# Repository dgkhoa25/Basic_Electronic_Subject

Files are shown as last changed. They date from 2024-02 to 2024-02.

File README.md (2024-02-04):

This project is created based on a subject with topic "Basic Electronic Project" (Đồ án Điện tử căn bản).

The name of project is "Designing model weighs mass to serve for mixing cement". 

******************************** ABSTRACT ***********************************************************

In order to help minimize errors in the process of providing materials for the consolidation process, this topic will provide a solution with a model of considering the forces serving that work.
The goal of this project is to help people limit errors, shortages, or excesses of materials by using mass sensors and digital signal processing systems to give the most accurate amount of materials 
needed to supply to the mixing systems. Some of the benefits of the project are: contributing to improving the accuracy of the quantity to be used and converting between different types of cement to be 
scanned automatically, saving users time, calculate, estimate. With this model, the system will process sequentially, so an error during the run is possible if a part of the input signal goes wrong.
Compared with the manual mixing method, this system will be more efficient in speed, with an accurate output volume of about 90%.

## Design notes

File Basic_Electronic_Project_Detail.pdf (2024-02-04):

BỘ GIÁO DỤC VÀ ĐÀO TẠO
TRƯỜNG ĐẠI HỌC CẦN THƠ
TRƯỜNG BÁCH KHOA
KHOA TỰ ĐỘNG HÓA
------🙢✧🙠------

BÁO CÁO
ĐỒ ÁN ĐIỆN TỬ CĂN BẢN
Mã học phần: KC331

### THIẾT KẾ MÔ HÌNH HỆ THỐNG CÂN ĐỊNH LƯỢNG PHỤC VỤ CHO PHA TRỘN XI MĂNG

CÁN BỘ HƯỚNG DẪN | SINH VIÊN THỰC HIỆN
TS. Nguyễn Hoàng Dũng | Nguyễn Đăng Khoa B1907027

Tháng 04/2023

Đồ án Điện tử căn bản | Trường Đại học Cần Thơ

### THIẾT KẾ MÔ HÌNH HỆ THỐNG CÂN ĐỊNH LƯỢNG PHỤC VỤ CHO PHA TRỘN XI MĂNG

Nguyễn Đăng Khoa¹

ABSTRACT

In order to help minimize errors in the process of providing materials for the consolidation process, this topic will provide a solution with a model of considering the forces serving that work. The goal of this project is to help people limit errors, shortages, or excesses of materials by using mass sensors and digital signal processing systems to give the most accurate amount of materials needed to supply to the mixing systems. Some of the benefits of the project are: contributing to improving the accuracy of the quantity to be used and converting between different types of cement to be scanned automatically, saving users time, calculate, estimate. With this model, the system will process sequentially, so an error during the run is possible if a part of the input signal goes wrong. Compared with the manual mixing method, this system will be more efficient in speed, with an accurate output volume of about 90%.
Keyword: mixed cement, mixing ratio cement, automation of production of concrete mix, microcontroller, STM32 Microcontroller, Loadcell sensor
Title: Designing model weighs mass to serve for mixing cement.

TÓM TẮT

Để giúp giảm thiểu sai sót trong quá trình cung cấp vật liệu cho quá trình pha trộn nên đề tài này sẽ đưa ra giải pháp với mô hình cân định lượng phục vụ cho việc đó. Mục tiêu của đề tài này là giúp con người hạn chế sai sót, thiếu hụt hay dư thừa nguyên liệu bằng việc dùng các cảm biến đo khối lượng và hệ thống xử lí tín hiệu số để đưa ra lượng vật tư chính xác nhất cần cung cấp cho hệ thống pha trộn. Một số lợi ích của đề tài mang lại là: góp phần nâng cao tính chính xác trong định lượng khối lượng cần dùng và chuyển đổi qua lại giữa các loại vữa xi măng một cách tự động, giúp người dùng tiết kiệm thời gian tính toán, ước lượng. Với mô hình này, hệ thống sẽ xử lí tuần tự nên việc xảy ra lỗi trong quá trình chạy là có nếu một bộ phận tín hiệu vào nào đó chạy sai. So với phương pháp pha trộn thủ công thì hệ thống này sẽ có hiệu quả hơn về tốc độ, khối lượng nguyên liệu đầu ra chính xác khoảng 90%.
Từ khóa: pha trộn xi măng, tỉ lệ pha trộn xi măng, tự động hóa sản xuất trong pha trộn bê tông, vi điều khiển, vi điều khiển STM32, cảm biến Loadcell.

### 1 GIỚI THIỆU

Trong công trình xây dựng, việc pha trộn xi măng là một khâu đặc thù và rất quan trọng. Bởi vì nó sẽ ảnh hưởng đến chất lượng cũng như tính an toàn về sau. Đề tài Hệ thống cân định lượng phục vụ cho pha trộn xi măng giúp vấn đề này trở nên hiệu quả hơn so với việc pha trộn thông qua ước tính nguyên liệu bằng thủ công. Hệ thống này sẽ ước tính chính xác lượng nguyên liệu cần để pha trộn và sau đó sẽ đưa đến máy chuyên dụng để tiến hành công đoạn tiếp theo.

1 Sinh viên lớp: Kỹ thuật Cơ điện tử A1 K45, Mã số SV: B1907027, Số ĐT: 0348967061, Email: khoab1907027@student.ctu.edu.vn

Với hệ thống này sẽ giúp hạn chế tối đa sai sót về tỉ lệ phần trăm giữa các thành phần có trong vữa và độ chính xác có thể lên đến 90% do sai số có thể dưới ±100 gram/lần cân.

Hiện nay việc đảm bảo chất lượng cho mỗi sản phẩm là việc rất quan trọng đối với các doanh nghiệp. Việc hiệu chỉnh các thông số đầu vào cũng như đầu ra phải dễ thực hiện và thuận lợi cho người sản xuất và người điều khiển trung tâm.
Công ty TNHH Đo lường và điều khiển Sơn Hòa đã sử dụng các mô-đun đo lường, cảm biến và các biến tần của các hãng nổi tiếng trên thế giới như Omron, Siemens, Delta, ABB,...[1] Đề tài có kế thừa nguyên lí gần giống với máy phối trộn nguyên liệu này và áp dụng cho việc thiết kế mô hình hệ thống của đề tài. Công ty cổ phần Ngôi Sao Kinh Bắc đã sản xuất các dòng cân điện tử như: cân ô tô, cần định lượng băng tải, cân đóng gói, cân silô... tốt nhất.[2] Để hoạt động chính xác, cân định lượng được thiết đặt tín hiệu dừng tắt dòng nguyên liệu.

Với các sản phẩm có sẵn trên thị trường, đề tài này sẽ thực hiện mô hình hóa đơn giản lại quá trình cân định lượng phục vụ cho pha trộn xi măng. Thông qua việc thực hiện đề tài giúp chúng ta có cái nhìn cụ thể cho một hệ thống pha trộn cũng như học hỏi thêm cách lập trình phần mềm cho một hệ thống nhiều trạng thái khác nhau.

### 2 PHƯƠNG PHÁP THỰC HIỆN

### 2.1 Tổng quan

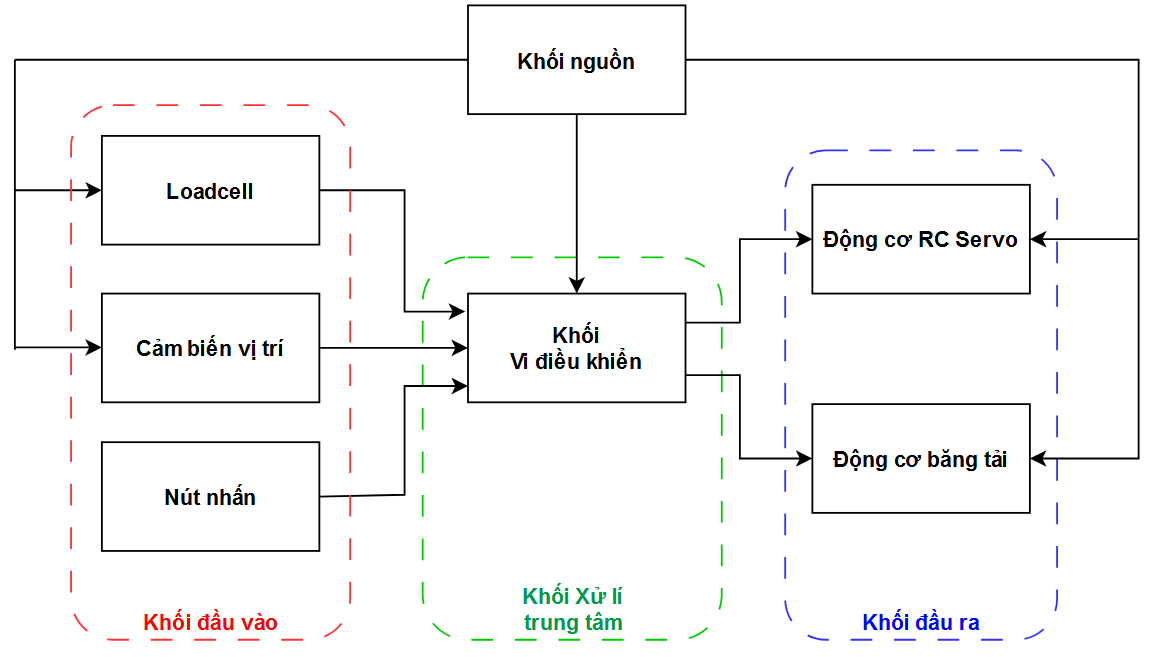
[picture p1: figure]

Hình 1: Sơ đồ khối của hệ thống

Hệ thống cân định lượng được xây dựng theo mô hình vào ra của các phần tử có trong hệ, bao gồm 3 khối chính theo như hình 1: khối đầu vào, khối xử lí trung tâm và khối đầu ra. Theo mô hình này hệ thống sẽ thực hiện tuần tự các chức năng đã được thiết lập sẵn.
Khối đầu vào: Khối này có chức năng thu thập các tín hiệu từ các cảm biến trọng lượng (Loadcell) và các cảm biến vị trí. Hình 2 là mạch cầu Wheaston thường được dùng để chuyển đổi sự thay đổi của điện trở thành sự thay đổi của điện áp trên đường chéo của cầu với điện áp ngõ ra được tính theo công thức 1. Ngoài ra còn có các nút nhấn khởi động hay dừng khẩn cấp cho hệ thống. Các cảm biến trọng lượng sẽ thực hiện chuyển đổi lực tác động vào phần thân Loadcell thành tín hiệu điện áp để vi điều khiển có thể xử lí.

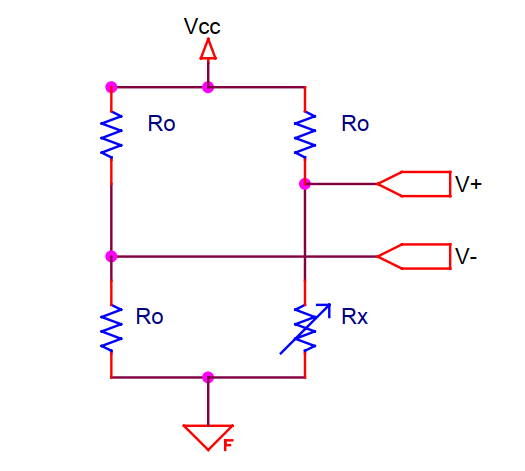
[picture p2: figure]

Hình 2: Sơ đồ nguyên lí mạch cầu Wheaston

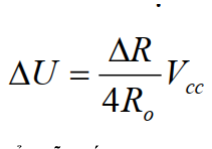
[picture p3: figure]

Hình 3: Biểu thức biểu diễn mối liên hệ giữa điện áp ngõ ra và điện trở
Các cảm biến vị trí sẽ xác định chính xác vị trí cần xả đúng loại nguyên liệu là cát, đá, xi măng hay nước. Cảm biến hồng ngoại có khả năng thích nghi với môi trường và có một cặp truyền nhận tia hồng ngoại.

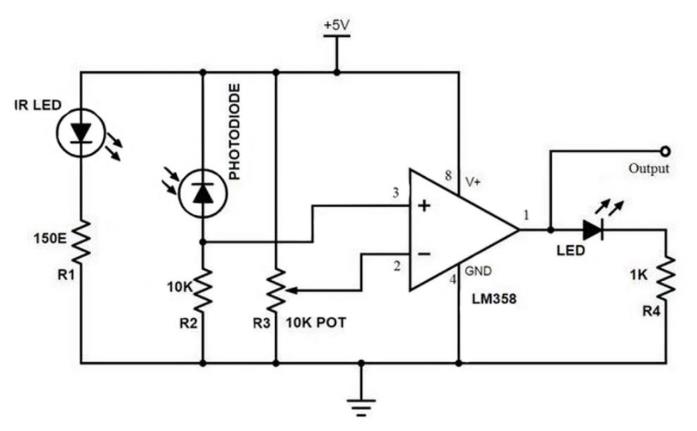
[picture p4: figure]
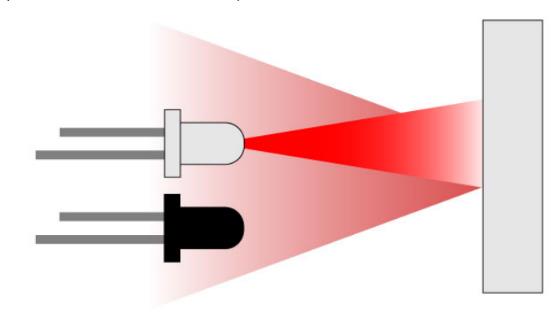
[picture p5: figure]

Hình 4: Sơ đồ nguyên lí của cảm biến quang hồng ngoại

(1)

Led phát hồng ngoại (IR LED) luôn luôn phát ra sóng ánh sáng có bước sóng hồng ngoại mắt người không thể nhìn thấy ánh sáng này, vì vậy người ta sử dụng led thu hồng ngoại, led thu hồng ngoại bình thường nó có nội trở rất lớn (vài trăm KΩ), khi led thu được tia hồng ngoại chiếu vào đủ lớn thì nội trở của nó giảm xuống (cỡ vài chục Ω). Khi gặp vật cản (hình 3), những chùm tia hồng ngoại gặp vật cản và phản xạ lại led thu làm led thu thay đổi giá trị điện trở. Ở đây chúng ta thấy cầu chia áp ở điện trở R2 và mắt thu hồng ngoại, sự thay đổi điện trở của mắt thu hồng ngoại dẫn đến điện áp đầu vào chân 3 Op-Amp cũng thay đổi. Khi khoảng cách càng gần, sự thay đổi càng lớn. Khi đó, điện áp đầu vào chân 3 Op-Amp được so sánh với giá trị điện áp không đổi gim trên biến trở R3, nếu điện áp chân 3 Op-Amp lớn hơn điện áp chân 2 Op-Amp thì Op-Amp xuất mức 1. Ngược lại nếu điện áp chân 3 Op-Amp nhỏ hơn điện áp chân 2 Op-Amp thì Op-Amp xuất mức 0.
Khối xử lí trung tâm: Khối này có nhiệm vụ tiếp nhận các tín hiệu đầu vào từ các cảm biến và nút nhấn để xử lí chúng thông qua vi điều khiển (Hình 5), sau đó cho ra tín hiệu ở đầu ra để điều khiển các thiết bị chấp hành cụ thể là các động cơ RC Servo làm cần gạt cho các cửa xả và động cơ băng chuyền.

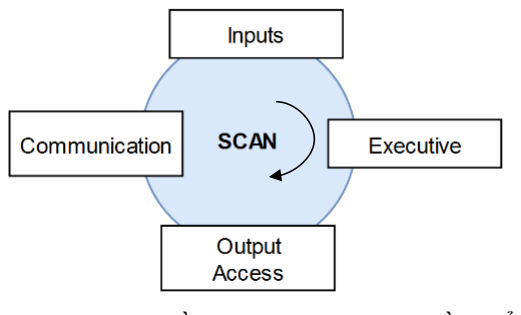
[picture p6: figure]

Hình 5: Sơ đồ thực thi trình tự của vi điều khiển
Khối đầu ra: Khối này có chức năng nhận tín hiệu ra từ khối trung tâm là vi điều khiển để điều khiển các cơ cấu chấp hành của hệ thống. Cơ cấu chấp hành bao gồm: động cơ RC Servo và động cơ DC của băng chuyền được điều khiển bằng xung PWM (Pulse Width Modulation). (Hình 6)

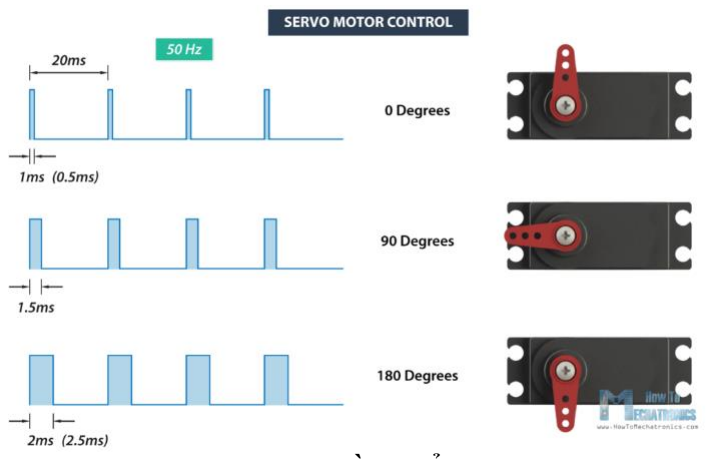
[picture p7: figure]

Hình 6: Nguyên lí điều khiển động cơ Servo

Bảng 1: Bảng thông số cấp phối vật liệu cho 1m³ của Mác 75 và Mác 200

Vật liệu

Mác

75 200

Xi măng PC30 | 296.03 Kg | 350 Kg
Cát | 1.12 m³ | 0.48 m³
Nước | 220 L | 189.6 L
Đá | | 0.899 m³
Áp dụng | Vữa xi măng | Bê tông

### 2.2 Thiết kế phần cứng

Với các chức năng đã trình bày trong sơ đồ khối, phần cứng mạch điện sẽ được thiết kế với các khối chức năng như sau: khối nguồn, khối vi điều khiển, khối giao tiếp cảm biến, khối nút nhấn và khối giao tiếp cơ cấu chấp hành.

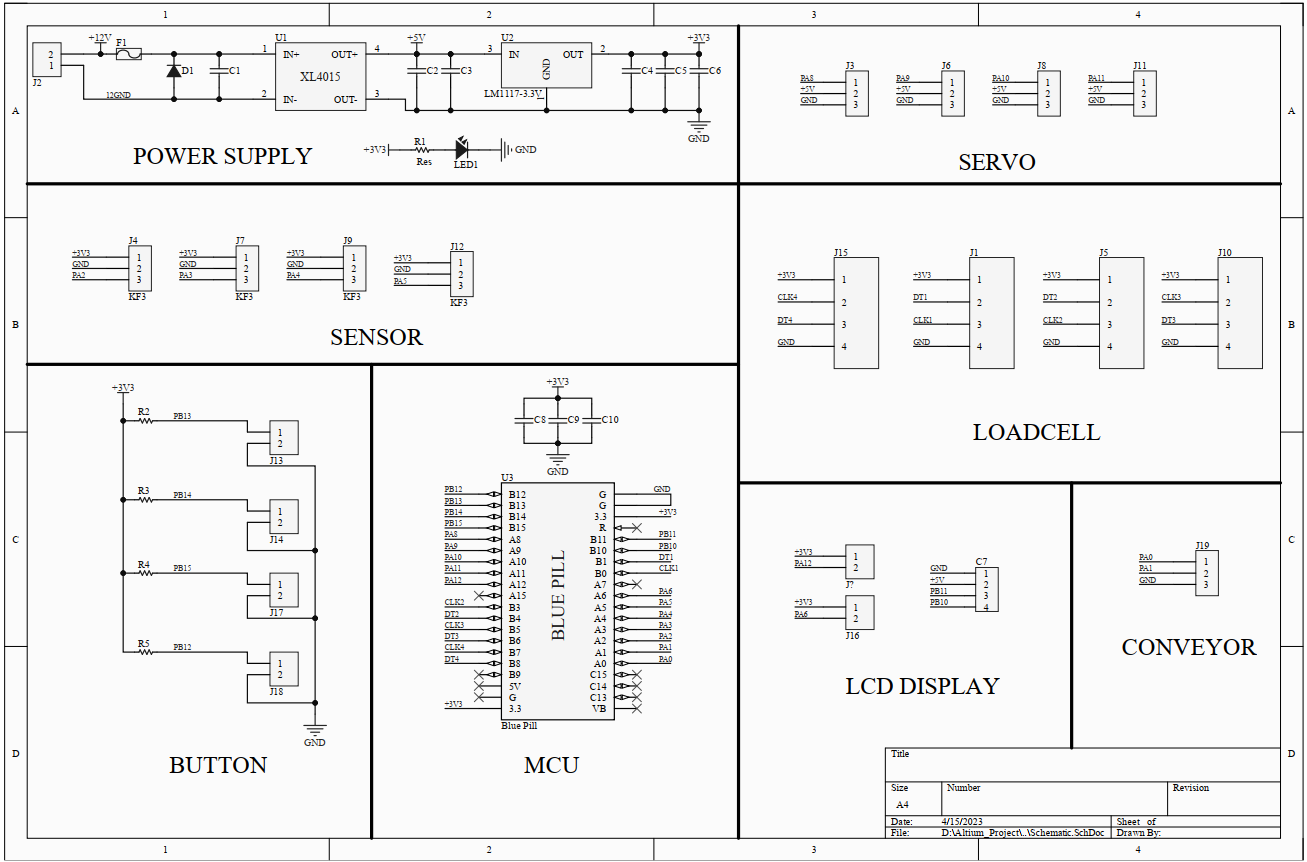
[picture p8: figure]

Hình 7: Sơ đồ nguyên lí mạch điện của hệ thống
− Khối nguồn: Sử dụng nguồn vào 12VDC cho toàn bộ mô hình hệ thống như hình
7. Để phù hợp với các mức điện áp của các linh kiện khác ta sẽ hạ áp thông qua 2 tầng. Tầng 1 sẽ thực hiện hạ áp từ 12VDC xuống 5VDC bằng mạch nguồn xung hạ áp DC - DC Buck LM2596. Tầng 2 sẽ tiếp tục hạ áp từ 5VDC xuống 3.3VDC bằng IC nguồn giảm áp LM1117 - 3.3. Mạch nguồn được thiết kế thêm một số linh kiện khác nhằm mục đích lọc nhiễu cho điện áp ra ổn định hơn và hạn chế quá dòng cho mạch.

− Khối vi điều khiển: Vi điều khiển STM32F103C8T6 được sử dụng làm bộ phận xử lí trung tâm của hệ thống. Với các chức năng đủ đáp ứng cho nhu cầu của hệ thống này như các chân vào ra đa dụng GPIO, bộ định thời Timer, bộ giao tiếp truyền thông I2C. STM32F103C8T6 đã được sử dụng rộng rãi trong vài năm trở lại đây với các ưu điểm nhiều hơn so với các dòng vi điều khiển đời cũ như AVR và 8051. STM32F103C8T6 là dòng vi điều khiển 32 bit, thuộc họ F1 của dòng chip STM32 hãng ST. Chip được thiết kế trên lõi ARM Cotex M3 với tốc độ tối đa 72 MHz. Bảng 2 sẽ trình bày thông số nổi bật của STM32F103C8T6.

Bảng 2: Bảng thông số nổi bật của vi điều khiển STM32F103C8T6

Bộ nhớ

Flash | 64 Kbytes
SRAM | 20 Kbytes

Bộ dao động

Nội | 8 MHz hoặc 40 kHz
Ngoại | 4 MHz – 20 MHz và 32.768 kHz (RTC)
Điện áp hoạt động | 2.0 – 3.6 V
Analog to Digital (ADC) | 2 bộ 12 bit
Timer | 7 bộ, có System Tick Timer

Giao tiếp

I2C | 2 bộ
USART | 3 bộ
SPIs | 2 bộ

− Khối giao tiếp cảm biến Loadcell: Thực hiện chuẩn giao tiếp đồng bộ qua hai dây Clock(CLK) và Data(DT). Do tín hiệu điện thế của Loadcell sinh ra rất nhỏ hàng mV từ công thức (1) nên cần một mạch khuếch đại điện áp ra và chuyển đổi từ tín hiệu tương tự (analog signal) sang tín hiệu số (digital signal) với 24 bit giá trị cho vi điều khiển xử lí.

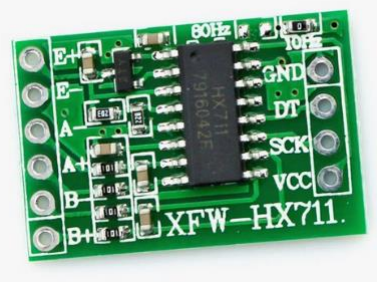
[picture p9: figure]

Hình 8: Module HX711
HX711 với tính năng biến đổi 24 bit kênh đôi Analog/Digital nhờ bộ khuếch đại cảm biến áp lực có sẵn trong một bảng mạch nhỏ gọn. Với bảng mạch này có sẵn các chân kết nối dễ dàng giữa vi điều khiển với Loadcell. Nó có 2 dây riêng biệt để giao tiếp với vi điều khiển là Data và Clock.

− Khối cơ cấu chấp hành: Các động cơ RC Servo được điều khiển thông qua độ rộng xung PWM để thay đổi được góc quay tương ứng. Sử dụng timer của STM32F103C8T6 để chọn kênh xuất xung cho động cơ với chu kì cố định là 20ms (50Hz). Động cơ DC của băng chuyền cũng được điều khiển thông qua PWM và mạch lái L298.

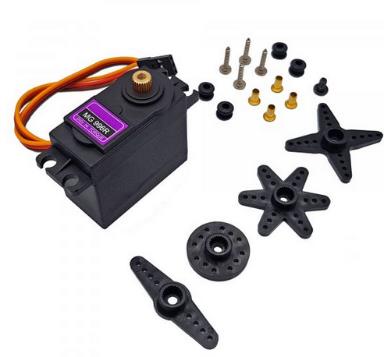
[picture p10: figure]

Hình 9: Động cơ Servo
Servo MG996R đây là bản nâng cấp từ servo MG995 về momen xoắn, tốc độ, lực kéo và độ chính xác. Momen làm việc : 11kg/cm (tại điện áp 6V), 9.4kg/cm (tại điện áp 4.8V).
− Khối nút nhấn: Các nút nhấn khởi động và dừng khẩn cấp để kích hoạt hệ thống. Bên cạnh đó còn có các nút nhấn chọn chế độ là Mác 75 và Mác 200. Ứng với mỗi Mác sẽ có cơ chế cân và số lần cân khác nhau.

### 2.3 Thiết kế phần mềm

### 2.3.1 Thiết kế giải thuật giao tiếp khối cảm biến Loadcell:

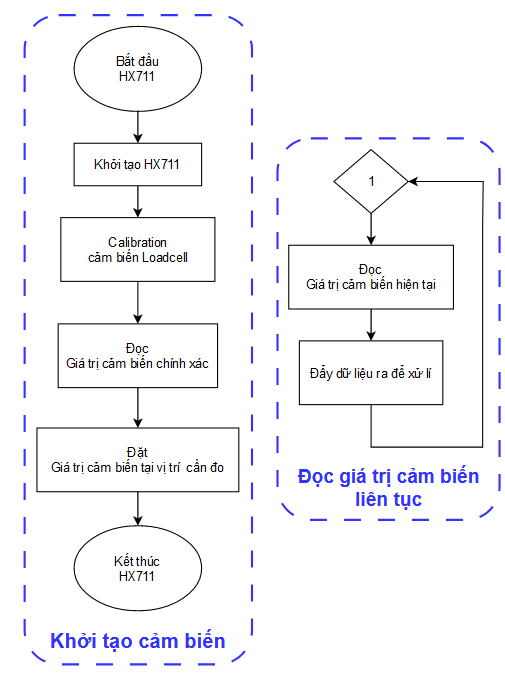
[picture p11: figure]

Hình 10: Lưu đồ khối cảm biến Loadcell
Giải thích lưu đồ: Chương trình chính bắt đầu với việc khởi tạo cảm biến Loadcell để thực hiện truyền dữ liệu về vi điều khiển. Sau đó tiếp tục thực hiện chuẩn hóa giá trị của cảm biến đúng theo trạng thái hiện tại(khi chưa thực hiện cân và cảm biến loadcell cân bằng). Cuối cùng đọc giá trị sau khi chuẩn hóa lần cuối để hoàn thành việc chuẩn hóa giá trị cho cảm biến và đặt giá trị tại đó làm chuẩn cho các lần đo lần sau. Để thực hiện lấy giá trị của cảm biến khi cân, ta sẽ quét liên tục với khoảng thời gian rất nhanh do vi điều khiển quy định. Dữ liệu đọc được từ cảm biến sẽ điều khiển các thiết bị cơ cấu chấp hành khác.

### 2.3.2 Thiết kế giải thuật điều khiển cơ cấu chấp hành:

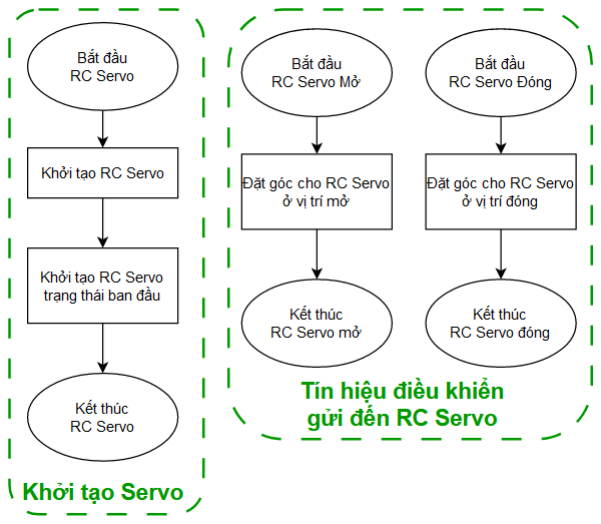
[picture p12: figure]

Hình 11: Lưu đồ khối điều khiển Servo
Giải thích lưu đồ: Chương trình chính sẽ khởi tạo các RC Servo để truyền tín hiệu từ vi điều khiển đến các RC Servo bằng phương pháp điều khiển độ rộng xung PWM và thực hiện đặt trạng thái ban đầu cho các động cơ Servo là ở vị trí đóng. Nếu có sự kiện yêu cầu đóng hoặc mở động cơ Servo thì sẽ gọi các hàm xử lí đóng hay mở ương ứng. Ở đây chỉ có hai góc đặt Servo tương ứng với hai trạng thái mở hoặc đóng.

### 2.3.3 Thiết kế giải thuật khối giao tiếp cảm biến vị trí:

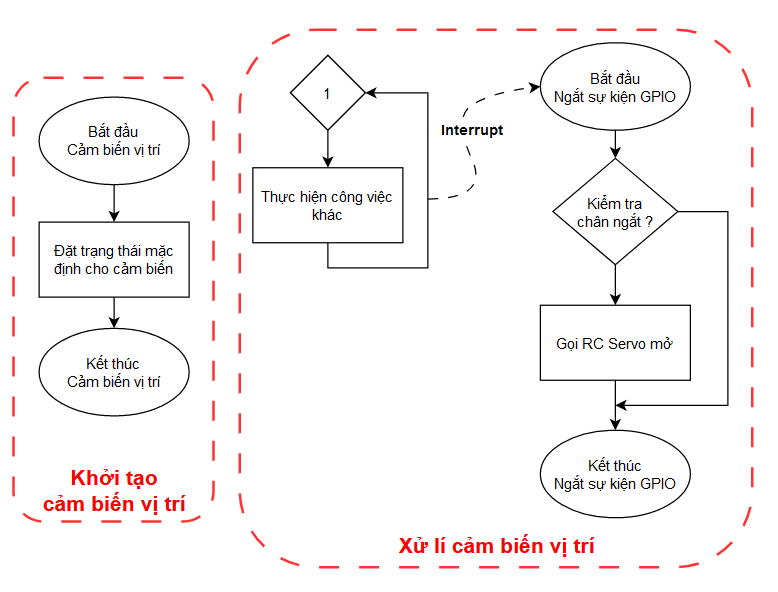
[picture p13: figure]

Hình 12: Lưu đồ khối xử lí cảm biến vị trí
Giải thích lưu đồ: Chương trình chính bắt đầu bằng việc khởi tạo tất cả các cảm biến ở trạng thái mặc định (chưa nhận vật cản). Khi vật đựng di chuyển đến cảm biến vị trí sẽ xảy ra ngắt ngoài ở chân GPIO tương ứng của vi điều khiển. Hàm xử lí ngắt sẽ được gọi để xử lí và điều khiển đóng mở cửa xả nguyên liệu bằng Servo. Nếu số lần cân đã đủ đối với mỗi loại nguyên liệu thì sẽ chuyển sang trạng thái cân nguyên liệu khác.

### 2.4 Thiết kế phần cứng mô hình:

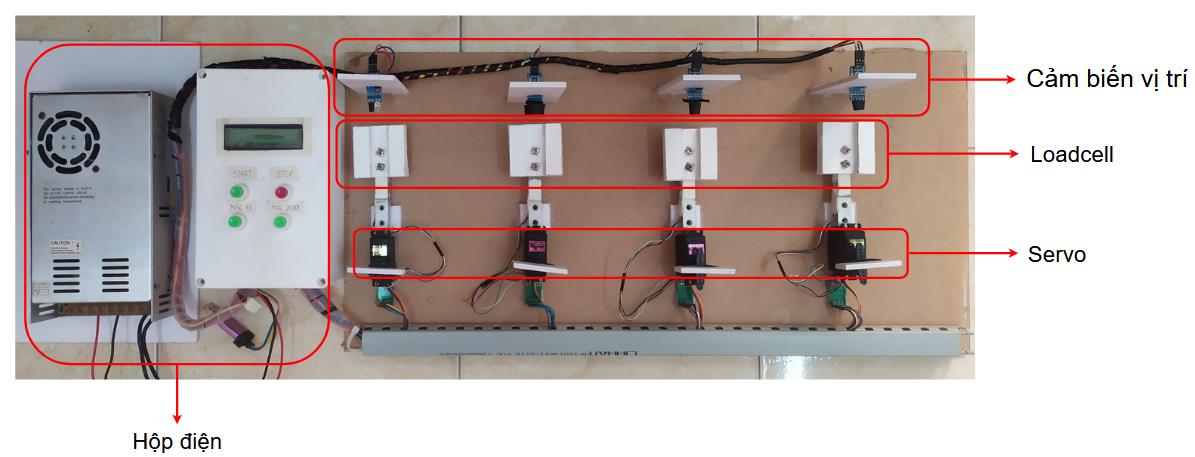
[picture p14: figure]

Hình 13: Mô hình hệ thống hoàn chỉnh
Hệ thống gồm có 4 phần chính: phần cảm biến vị trí vật cản, phần cảm biến Loadcell, phần động cơ Servo và phần hộp điện.

### 2.4.1 Thiết kế phần khung cảm biến vật cản:

Các khung giá đỡ cảm biến gồm 4 cái dựng đối diện cảm biến Loadcell nhằm mục đích xác định chính xác vị trí của vật đựng di chuyển đến. Khoảng cách để cảm biến nhận diện được vật đựng là khoảng 1 - 2 cm. Các cảm biến được cố định bởi các tấm phôm bằng nhựa và dán keo silicon.

### 2.4.2 Thiết kế phần khung cảm biến trọng lượng Loadcell:

Giá đỡ cảm biến loadcell được cố định cứng một đầu vào khung nền của hệ thống và để tự do ở đầu còn lại. Ở đầu còn lại này sẽ gắn tấm phôm để tăng kích thước chứa vật đựng không bị nghiêng lắc trong lúc cân.
Mạch khuếch đại và chuyển đổi tín hiệu điện áp HX711 được cố định cứng vào khung nền bằng keo silicon và được đặt gần với cảm biến loadcell nhằm hạn chế sai số trong quá trình truyền tín hiệu đến mạch.

### 2.4.3 Thiết kế phần khung đóng mở cửa nguyên liệu với động cơ Servo:

Hệ thống cần gạt đóng mở cửa cung cấp nguyên liệu được mô hình hóa lại bằng cách sử dụng động cơ Servo. Các động cơ sẽ có nhiệm vụ chính là mở ra khi có vật chứa đựng đến vị trí tương ứng và đóng lại khi lượng nguyên liệu đã đủ. Tín hiệu điều khiển các động cơ này phụ thuộc vào khối xử lí trung tâm.

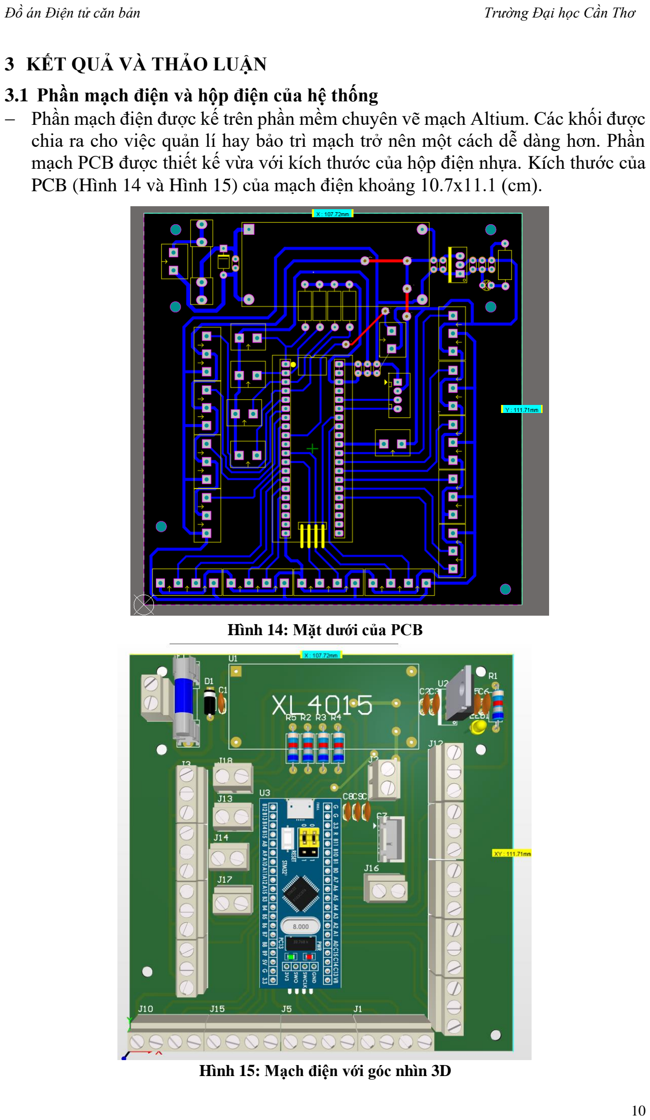
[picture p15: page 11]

### 3 KẾT QUẢ VÀ THẢO LUẬN

### 3.1 Phần mạch điện và hộp điện của hệ thống

− Phần mạch điện được kế trên phần mềm chuyên vẽ mạch Altium. Các khối được chia ra cho việc quản lí hay bảo trì mạch trở nên một cách dễ dàng hơn. Phần mạch PCB được thiết kế vừa với kích thước của hộp điện nhựa. Kích thước của PCB (Hình 14 và Hình 15) của mạch điện khoảng 10.7x11.1 (cm).

Hình 14: Mặt dưới của PCB

Hình 15: Mạch điện với góc nhìn 3D

− Phần hộp điện (Hình 16) bằng nhựa ABS với chất liệu chịu được nhiệt độ của môi trường. Trên bề mặt của hộp bao gồm các phím chức năng và màn hình hiển thị LCD. Về phím chức năng gồm có 4 phím: phím bắt đầu hệ thống (START), phím dừng hệ thống (STOP), phím chọn chế độ Mác 75 và phím chọn chế độ Mác 200. Còn phần hiển thị thông qua LCD sẽ cho hiển thị lên các thông số ở màn hình chính là: chế độ Mác hiện tại, khối lượng của nguyên liệu đang đổ vào vật chứa và số lần đã cân với mỗi nguyên liệu.

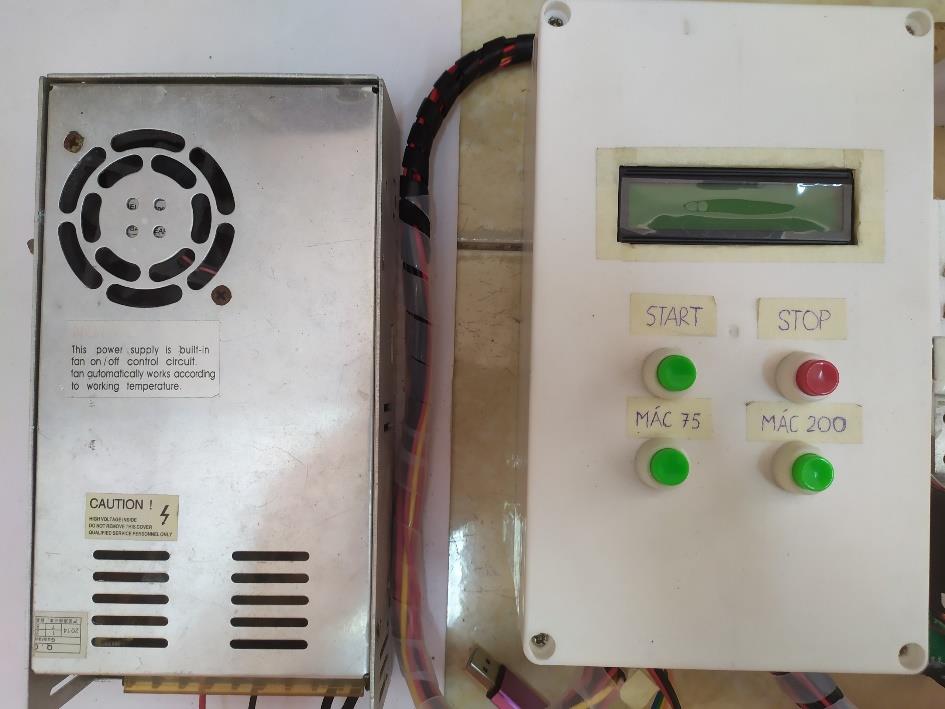
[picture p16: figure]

Hình 16: Hộp điện thực tế

### 3.2 Phần mô hình hệ thống và lưu đồ giải thuật chương trình:

Phần mô hình được thiết kế mô phỏng lại quá trình cân định lượng ở dạng tĩnh kết hợp với băng tải. Phần mô hình gồm có 3 khu vực chính là: khu vực lắp cảm biến vị trí, khu vực lắp cảm biến Loadcell và khu vực lắp động cơ Servo. Hệ thống sẽ tiến hành cân từ phải qua trái với lần lượt thứ tự cân mỗi nguyên liệu được cài đặt sẵn trong chương trình và số lần cân một nguyên liệu cũng sẽ được thiết lập sẵn, nếu số lần cân của một nguyên liệu đã đủ thì sẽ chuyển sang chu trình cân nguyên liệu khác. Quá trình cân được cài đặt lần lượt như sau:

− Mác 75 với chu trình cân là:

- Chu trình 1: Cát
- Chu trình 2: Xi măng
- Chu trình 3: Nước

− Mác 200 với chu trình cân là:

- Chu trình 1: Cát
- Chu trình 2: Xi măng
- Chu trình 3: Đá
- Chu trình 4: Nước

Lưu đồ giải thuật của chương trình:

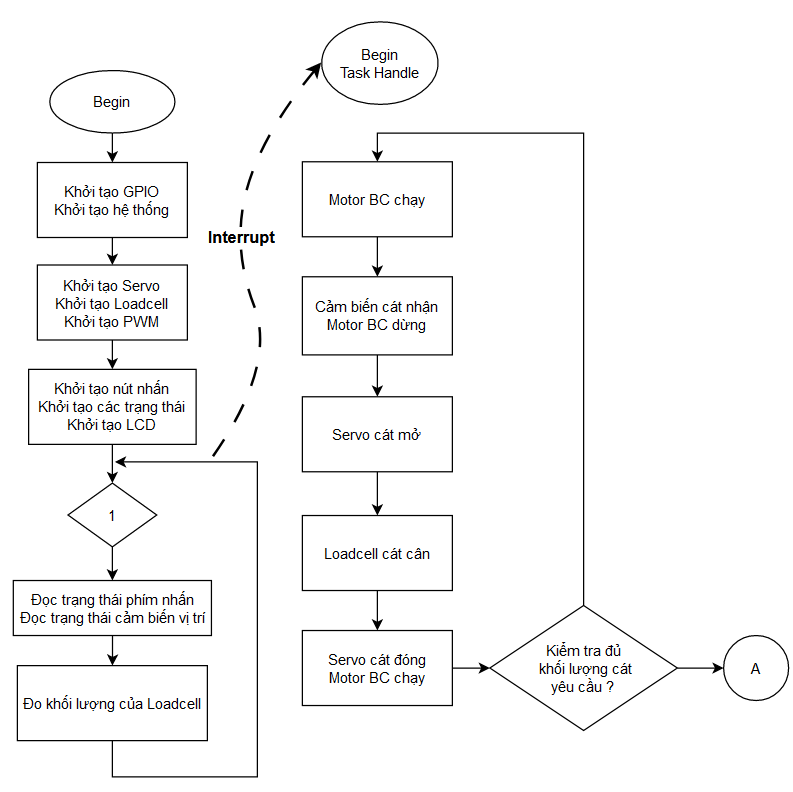
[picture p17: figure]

Hình 17: Lưu đồ giải thuật chương trình chính phần 1

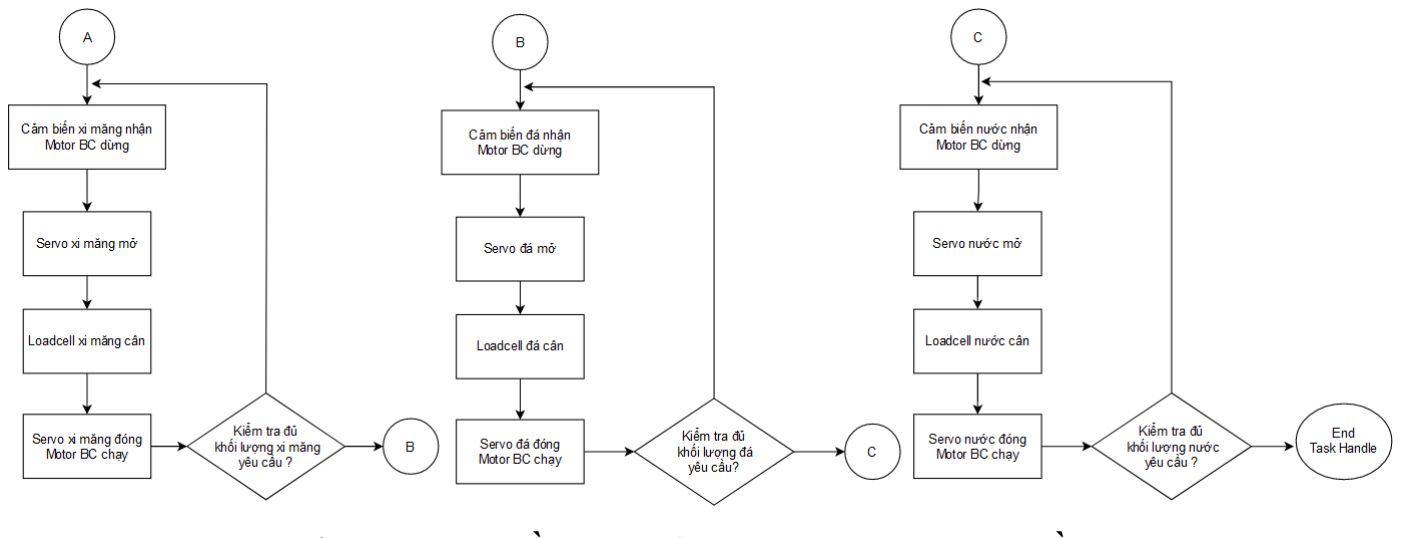
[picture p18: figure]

Hình 18: Lưu đồ giải thuật chương trình chính phần 2
Kết quả đã thực hiện được biểu diễn chi tiết qua các thông số sau trong bảng 3:

Bảng 3: Bảng thông số định lượng của toàn bộ hệ thống

Chức năng

Cân tự động
Hiển thị thông số theo thời gian thực
Thời gian đáp ứng về mặt chương trình | Nhanh, không trì hoãn
Khả năng giới hạn Loadcell | < 1 Kg
Số lần cân | 1 lần
Sai số cân | ±3 gram
Bảo trì và nâng cấp | Dễ

Theo các kết quả trên thì đã đáp ứng được một phần yêu cầu đặt ra. Còn thiếu một số thiết bị để bám sát với thực tế hơn. Tốc độ của toàn bộ hệ thống phụ thuộc vào tốc độ băng tải và đường kính của cấp nguyên liệu là chủ yếu.

Hệ thống chạy đúng với các thông số đã thiết lập sẵn nhưng vẫn còn một số trường hợp bị treo hệ thống là do chương trình viết chưa được tối ưu, hiệu quả. Hệ thống cần phải chia ra những phần tử nhỏ hơn để tiện thao tác và khắc phục sai sót.

### 4 KẾT LUẬN VÀ ĐỀ NGHỊ

− Phương pháp thiết kế đã đúng được một phần của mục tiêu là thiết kế một hệ thống cân định lượng ở dạng tĩnh để phục vụ cho pha trộn xi măng. Với thiết kế dưới dạng mô hình này về giải thuật chương trình sẽ gần giống nhất với thực tế. Khi áp dụng vào thực tế chúng ta chỉ cần chỉnh sửa lại một chút và thêm giải thuật để điều khiển hiệu quả và tối ưu hơn.
− Ưu điểm: Hệ thống này đã biểu diễn một cách khái quát cho hệ thống cân lớn hơn. Ngoài ra phục vụ cho cân định lượng nguyên liệu xây dựng thì có thể chuyển sang cân nguyên liệu khác một cách dễ dàng. Khắc phục được tình trạng thao tác bằng tay quá nhiều trên bảng điều khiển.
− Nhược điểm: Hệ thống chỉ được thiết kế dưới dạng mô hình nên còn thiếu một số phần để trở nên hoàn chỉnh. Hệ thống sẽ có giới hạn cân nên phải chia ra nhiều lần cân điều đó dẫn đến sai số tăng và làm chậm quá trình cung cấp nguyên liệu đến đầu ra.
− Để khắc phục được nhược điểm trên, cần phải thêm băng chuyền để mô phỏng chính xác quá trình cân cũng như khả năng đáp ứng của hệ thống điều khiển. Sử dụng Loadcell có giới hạn cân lớn hơn để cân nhằm mục đích hạn chế lại số lần cân một nguyên liệu. Sử dụng các cảm biến có độ bền và độ chính xác cao để tối ưu khả năng chính xác.

CÁM ƠN

Qua đề tài này, em xin cảm ơn thầy Nguyễn Hoàng Dũng đã cho em cơ hội để thử sức với việc lập trình một hệ thống nhúng có nhiều trạng thái. Nhờ có sự giúp đỡ và đóng góp ý kiến từ thầy mà em mới có thể hoàn thành đồ án tốt nhất có thể. Em xin cảm ơn bạn bè đã hỗ trợ nhiệt tình cho em trong suốt quá trình làm đồ án này. Cuối cùng em gửi lời cảm ơn đến bạn bè đã đọc và đóng góp ý kiến để em hoàn chỉnh lại đồ án tốt hơn.

TÀI LIỆU THAM KHẢO

[1] Công ty TNHH Đo lường và điều khiển Sơn Hòa, 2015. Cân định lượng, phối trộn nguyên liệu. Truy cập từ https://daychuyentudong.vn/can-dinh-luong-phoi-tron-nguyen-lieu vào ngày 13 tháng 11 năm 2022.
[2] Công ty Cổ Phần Ngôi Sao Kinh Bắc, 2023. Cân định lượng phối trộn nguyên liệu tại Bắc Ninh. Truy cập từ https://candientu24h.vn/can-dinh-luong-phoi-tron-nguyen-lieu-tai-bac-ninh.html (https://candientu24h.vn/can-dinh-luong-phoi-tron-nguyen-lieu-tai-bac-ninh.html) vào ngày 13 tháng 11 năm 2022.
[3] Yifeng Zhu, 2018. Embedded Systems with ARM Cortex-M Microcontrollers in Assembly Language and C. E-Man Press LLC, 711 trang.
[4] Muhammad Tahir và Kashif Javed, 2017. ARM microprocessor systems _ Cortex-M architecture, programming, and interfacing. Taylor and Francis Group, 651 trang.

[5] Công ty TNHH Vật liệu Xây dựng mới Tenzi, 2022. Trộn xi măng với nước cùng tỷ lệ chuẩn nhất. Truy cập từ https://tenzi.com.vn/tron-xi-mang-voi-nuoc-cung-ty-le-chuan-nhat/ (https://tenzi.com.vn/tron-xi-mang-voi-nuoc-cung-ty-le-chuan-nhat/) vào ngày 16 tháng 12 năm 2022
[6] Công ty TNHH Vietnamarch, 2016. Tỷ lệ trộn bê tông mác 200 trong xây dựng. Truy cập từ https://vietnamarch.com.vn/ty-le-tron-be-tong-mac-200-trong-xay-dung/ vào ngày 13 tháng 04 năm 2023.
[7] Công ty TNHH Vật liệu xây dựng Sài Gòn CMC, 2020. 1 bao xi măng trộn bao nhiêu cát là chuẩn nhất. Truy cập từ https://khocatdaxaydungcmc.com/1-bao-xi-mang-tron-bao-nhieu-cat/ (https://khocatdaxaydungcmc.com/1-bao-xi-mang-tron-bao-nhieu-cat/) vào ngày 13 tháng 04 năm 2023.
[8] Khuê Nguyễn Creator, 2021. Lập trình STM32 với LCD I2C sử dụng module PCF8574. Truy cập từ https://khuenguyencreator.com/lap-trinh-stm32-voi-lcd-i2c-su-dung-module-pcf8574/ (https://khuenguyencreator.com/lap-trinh-stm32-voi-lcd-i2c-su-dung-module-pcf8574/) vào ngày 15 tháng 02 năm 2023.
[9] | Nima | Askari, | 2020. | HX711 | Library | for | STM32. | Truy | cập | từ
https://github.com/nimaltd/HX711 vào ngày 10 tháng 11 năm 2022.

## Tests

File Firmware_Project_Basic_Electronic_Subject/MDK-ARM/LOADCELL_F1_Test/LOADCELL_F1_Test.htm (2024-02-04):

# Static Call Graph for image LOADCELL_F1_Test\LOADCELL_F1_Test.axf

#<CALLGRAPH># ARM Linker, 5060960: Last Updated: Sat Feb 03 15:13:21 2024

### Maximum Stack Usage = 324 bytes + Unknown(Functions without stacksize, Cycles, Untraceable Function Pointers)

### Call chain for Maximum Stack Depth:

_printf_f ⇒ _printf_fp_dec ⇒ _printf_fp_dec_real ⇒ _fp_digits ⇒ _btod_etento ⇒ _btod_emul ⇒ _e2e

### Functions with no stack information

- __user_initial_stackheap

### Mutually Recursive functions

- ADC1_2_IRQHandler ⇒ ADC1_2_IRQHandler
- BusFault_Handler ⇒ BusFault_Handler
- HardFault_Handler ⇒ HardFault_Handler
- MemManage_Handler ⇒ MemManage_Handler
- NMI_Handler ⇒ NMI_Handler
- UsageFault_Handler ⇒ UsageFault_Handler

### Function Pointers

- ADC1_2_IRQHandler from startup_stm32f103xb.o(.text) referenced from startup_stm32f103xb.o(RESET)
- BusFault_Handler from stm32f1xx_it.o(i.BusFault_Handler) referenced from startup_stm32f103xb.o(RESET)
- CAN1_RX1_IRQHandler from startup_stm32f103xb.o(.text) referenced from startup_stm32f103xb.o(RESET)
- CAN1_SCE_IRQHandler from startup_stm32f103xb.o(.text) referenced from startup_stm32f103xb.o(RESET)
- DMA1_Channel1_IRQHandler from startup_stm32f103xb.o(.text) referenced from startup_stm32f103xb.o(RESET)
- DMA1_Channel2_IRQHandler from startup_stm32f103xb.o(.text) referenced from startup_stm32f103xb.o(RESET)
- DMA1_Channel3_IRQHandler from startup_stm32f103xb.o(.text) referenced from startup_stm32f103xb.o(RESET)
- DMA1_Channel4_IRQHandler from startup_stm32f103xb.o(.text) referenced from startup_stm32f103xb.o(RESET)
- DMA1_Channel5_IRQHandler from startup_stm32f103xb.o(.text) referenced from startup_stm32f103xb.o(RESET)
- DMA1_Channel6_IRQHandler from startup_stm32f103xb.o(.text) referenced from startup_stm32f103xb.o(RESET)
- DMA1_Channel7_IRQHandler from startup_stm32f103xb.o(.text) referenced from startup_stm32f103xb.o(RESET)
- DebugMon_Handler from stm32f1xx_it.o(i.DebugMon_Handler) referenced from startup_stm32f103xb.o(RESET)
- EXTI0_IRQHandler from startup_stm32f103xb.o(.text) referenced from startup_stm32f103xb.o(RESET)
- EXTI15_10_IRQHandler from startup_stm32f103xb.o(.text) referenced from startup_stm32f103xb.o(RESET)
- EXTI1_IRQHandler from startup_stm32f103xb.o(.text) referenced from startup_stm32f103xb.o(RESET)
- EXTI2_IRQHandler from startup_stm32f103xb.o(.text) referenced from startup_stm32f103xb.o(RESET)
- EXTI3_IRQHandler from startup_stm32f103xb.o(.text) referenced from startup_stm32f103xb.o(RESET)
- EXTI4_IRQHandler from startup_stm32f103xb.o(.text) referenced from startup_stm32f103xb.o(RESET)
- EXTI9_5_IRQHandler from startup_stm32f103xb.o(.text) referenced from startup_stm32f103xb.o(RESET)
- FLASH_IRQHandler from startup_stm32f103xb.o(.text) referenced from startup_stm32f103xb.o(RESET)
- HardFault_Handler from stm32f1xx_it.o(i.HardFault_Handler) referenced from startup_stm32f103xb.o(RESET)
- I2C1_ER_IRQHandler from startup_stm32f103xb.o(.text) referenced from startup_stm32f103xb.o(RESET)
- I2C1_EV_IRQHandler from startup_stm32f103xb.o(.text) referenced from startup_stm32f103xb.o(RESET)
- I2C2_ER_IRQHandler from startup_stm32f103xb.o(.text) referenced from startup_stm32f103xb.o(RESET)
- I2C2_EV_IRQHandler from startup_stm32f103xb.o(.text) referenced from startup_stm32f103xb.o(RESET)
- MemManage_Handler from stm32f1xx_it.o(i.MemManage_Handler) referenced from startup_stm32f103xb.o(RESET)
- NMI_Handler from stm32f1xx_it.o(i.NMI_Handler) referenced from startup_stm32f103xb.o(RESET)
- PVD_IRQHandler from startup_stm32f103xb.o(.text) referenced from startup_stm32f103xb.o(RESET)
- PendSV_Handler from stm32f1xx_it.o(i.PendSV_Handler) referenced from startup_stm32f103xb.o(RESET)
- RCC_IRQHandler from startup_stm32f103xb.o(.text) referenced from startup_stm32f103xb.o(RESET)
- RTC_Alarm_IRQHandler from startup_stm32f103xb.o(.text) referenced from startup_stm32f103xb.o(RESET)
- RTC_IRQHandler from startup_stm32f103xb.o(.text) referenced from startup_stm32f103xb.o(RESET)
- Reset_Handler from startup_stm32f103xb.o(.text) referenced from startup_stm32f103xb.o(RESET)
- SPI1_IRQHandler from startup_stm32f103xb.o(.text) referenced from startup_stm32f103xb.o(RESET)
- SPI2_IRQHandler from startup_stm32f103xb.o(.text) referenced from startup_stm32f103xb.o(RESET)
- SVC_Handler from stm32f1xx_it.o(i.SVC_Handler) referenced from startup_stm32f103xb.o(RESET)
- SysTick_Handler from stm32f1xx_it.o(i.SysTick_Handler) referenced from startup_stm32f103xb.o(RESET)
- SystemInit from system_stm32f1xx.o(i.SystemInit) referenced from startup_stm32f103xb.o(.text)
- TAMPER_IRQHandler from startup_stm32f103xb.o(.text) referenced from startup_stm32f103xb.o(RESET)
- TIM1_BRK_IRQHandler from startup_stm32f103xb.o(.text) referenced from startup_stm32f103xb.o(RESET)
- TIM1_CC_IRQHandler from startup_stm32f103xb.o(.text) referenced from startup_stm32f103xb.o(RESET)
- TIM1_TRG_COM_IRQHandler from startup_stm32f103xb.o(.text) referenced from startup_stm32f103xb.o(RESET)
- TIM1_UP_IRQHandler from startup_stm32f103xb.o(.text) referenced from startup_stm32f103xb.o(RESET)
- TIM2_IRQHandler from startup_stm32f103xb.o(.text) referenced from startup_stm32f103xb.o(RESET)
- TIM3_IRQHandler from startup_stm32f103xb.o(.text) referenced from startup_stm32f103xb.o(RESET)
- TIM4_IRQHandler from startup_stm32f103xb.o(.text) referenced from startup_stm32f103xb.o(RESET)
- USART1_IRQHandler from startup_stm32f103xb.o(.text) referenced from startup_stm32f103xb.o(RESET)
- USART2_IRQHandler from startup_stm32f103xb.o(.text) referenced from startup_stm32f103xb.o(RESET)
- USART3_IRQHandler from startup_stm32f103xb.o(.text) referenced from startup_stm32f103xb.o(RESET)
- USBWakeUp_IRQHandler from startup_stm32f103xb.o(.text) referenced from startup_stm32f103xb.o(RESET)
- USB_HP_CAN1_TX_IRQHandler from startup_stm32f103xb.o(.text) referenced from startup_stm32f103xb.o(RESET)
- USB_LP_CAN1_RX0_IRQHandler from startup_stm32f103xb.o(.text) referenced from startup_stm32f103xb.o(RESET)
- UsageFault_Handler from stm32f1xx_it.o(i.UsageFault_Handler) referenced from startup_stm32f103xb.o(RESET)
- WWDG_IRQHandler from startup_stm32f103xb.o(.text) referenced from startup_stm32f103xb.o(RESET)
- __main from __main.o(!!!main) referenced from startup_stm32f103xb.o(.text)
- _get_lc_ctype from lc_ctype_c.o(locale$$code) referenced from rt_ctype_table.o(.text)
- _printf_input_char from _printf_char_common.o(.text) referenced from _printf_char_common.o(.text)
- _sputc from _sputc.o(.text) referenced from vsprintf.o(.text)

### Global Symbols

__main (Thumb, 8 bytes, Stack size 0 bytes, __main.o(!!!main))

[Calls]

- >> __rt_entry
- >> __scatterload

__scatterload (Thumb, 0 bytes, Stack size unknown bytes, __scatter.o(!!!scatter))

[Called By]

- >> __main

__scatterload_rt2 (Thumb, 44 bytes, Stack size unknown bytes, __scatter.o(!!!scatter), UNUSED)

[Calls]

- >> __rt_entry

__scatterload_rt2_thumb_only (Thumb, 0 bytes, Stack size unknown bytes, __scatter.o(!!!scatter), UNUSED)

__scatterload_null (Thumb, 0 bytes, Stack size unknown bytes, __scatter.o(!!!scatter), UNUSED)

__scatterload_copy (Thumb, 26 bytes, Stack size unknown bytes, __scatter_copy.o(!!handler_copy), UNUSED)

[Calls]

- >> __scatterload_copy

[Called By]

- >> __scatterload_copy

__scatterload_zeroinit (Thumb, 28 bytes, Stack size unknown bytes, __scatter_zi.o(!!handler_zi), UNUSED)

_printf_n (Thumb, 0 bytes, Stack size unknown bytes, _printf_n.o(.ARM.Collect$$_printf_percent$$00000001))

[Calls]

- >> _printf_charcount

_printf_percent (Thumb, 0 bytes, Stack size unknown bytes, _printf_percent.o(.ARM.Collect$$_printf_percent$$00000000))

[Called By]

- >> __printf

_printf_p (Thumb, 0 bytes, Stack size unknown bytes, _printf_p.o(.ARM.Collect$$_printf_percent$$00000002))

[Stack]

- Max Depth = 64 + Unknown Stack Size
- Call Chain = _printf_p ⇒ _printf_hex_ptr ⇒ _printf_longlong_hex ⇒ _printf_int_common ⇒ _printf_post_padding

[Calls]

- >> _printf_hex_ptr

_printf_f (Thumb, 0 bytes, Stack size unknown bytes, _printf_f.o(.ARM.Collect$$_printf_percent$$00000003))

[Stack]

- Max Depth = 324 + Unknown Stack Size
- Call Chain = _printf_f ⇒ _printf_fp_dec ⇒ _printf_fp_dec_real ⇒ _fp_digits ⇒ _btod_etento ⇒ _btod_emul ⇒ _e2e

[Calls]

- >> _printf_fp_dec

_printf_e (Thumb, 0 bytes, Stack size unknown bytes, _printf_e.o(.ARM.Collect$$_printf_percent$$00000004))

[Stack]

- Max Depth = 324 + Unknown Stack Size
- Call Chain = _printf_e ⇒ _printf_fp_dec ⇒ _printf_fp_dec_real ⇒ _fp_digits ⇒ _btod_etento ⇒ _btod_emul ⇒ _e2e

[Calls]

- >> _printf_fp_dec

_printf_g (Thumb, 0 bytes, Stack size unknown bytes, _printf_g.o(.ARM.Collect$$_printf_percent$$00000005))

[Stack]

- Max Depth = 324 + Unknown Stack Size
- Call Chain = _printf_g ⇒ _printf_fp_dec ⇒ _printf_fp_dec_real ⇒ _fp_digits ⇒ _btod_etento ⇒ _btod_emul ⇒ _e2e

[Calls]

- >> _printf_fp_dec

_printf_a (Thumb, 0 bytes, Stack size unknown bytes, _printf_a.o(.ARM.Collect$$_printf_percent$$00000006))

[Stack]

- Max Depth = 112 + Unknown Stack Size
- Call Chain = _printf_a ⇒ _printf_fp_hex ⇒ _printf_fp_hex_real ⇒ _printf_fp_infnan ⇒ _printf_post_padding

[Calls]

- >> _printf_fp_hex

_printf_ll (Thumb, 0 bytes, Stack size unknown bytes, _printf_ll.o(.ARM.Collect$$_printf_percent$$00000007))

_printf_i (Thumb, 0 bytes, Stack size unknown bytes, _printf_i.o(.ARM.Collect$$_printf_percent$$00000008))

[Stack]

- Max Depth = 72 + Unknown Stack Size
- Call Chain = _printf_i ⇒ _printf_int_dec ⇒ _printf_int_common ⇒ _printf_post_padding

[Calls]

- >> _printf_int_dec

_printf_d (Thumb, 0 bytes, Stack size unknown bytes, _printf_d.o(.ARM.Collect$$_printf_percent$$00000009))

[Stack]

- Max Depth = 72 + Unknown Stack Size
- Call Chain = _printf_d ⇒ _printf_int_dec ⇒ _printf_int_common ⇒ _printf_post_padding

[Calls]

- >> _printf_int_dec

_printf_u (Thumb, 0 bytes, Stack size unknown bytes, _printf_u.o(.ARM.Collect$$_printf_percent$$0000000A))

[Stack]

- Max Depth = 72 + Unknown Stack Size
- Call Chain = _printf_u ⇒ _printf_int_dec ⇒ _printf_int_common ⇒ _printf_post_padding

[Calls]

- >> _printf_int_dec

_printf_o (Thumb, 0 bytes, Stack size unknown bytes, _printf_o.o(.ARM.Collect$$_printf_percent$$0000000B))

[Stack]

- Max Depth = 64 + Unknown Stack Size
- Call Chain = _printf_o ⇒ _printf_int_oct ⇒ _printf_longlong_oct ⇒ _printf_int_common ⇒ _printf_post_padding

[Calls]

- >> _printf_int_oct

_printf_x (Thumb, 0 bytes, Stack size unknown bytes, _printf_x.o(.ARM.Collect$$_printf_percent$$0000000C))

[Stack]

- Max Depth = 80 + Unknown Stack Size
- Call Chain = _printf_x ⇒ _printf_int_hex ⇒ _printf_longlong_hex ⇒ _printf_int_common ⇒ _printf_post_padding

[Calls]

- >> _printf_int_hex

_printf_lli (Thumb, 0 bytes, Stack size unknown bytes, _printf_lli.o(.ARM.Collect$$_printf_percent$$0000000D))

[Stack]

- Max Depth = 72 + Unknown Stack Size
- Call Chain = _printf_lli ⇒ _printf_longlong_dec ⇒ _printf_int_common ⇒ _printf_post_padding

[Calls]

- >> _printf_longlong_dec

_printf_lld (Thumb, 0 bytes, Stack size unknown bytes, _printf_lld.o(.ARM.Collect$$_printf_percent$$0000000E))

[Stack]

- Max Depth = 72 + Unknown Stack Size
- Call Chain = _printf_lld ⇒ _printf_longlong_dec ⇒ _printf_int_common ⇒ _printf_post_padding

[Calls]

- >> _printf_longlong_dec

_printf_llu (Thumb, 0 bytes, Stack size unknown bytes, _printf_llu.o(.ARM.Collect$$_printf_percent$$0000000F))

[Stack]

- Max Depth = 72 + Unknown Stack Size
- Call Chain = _printf_llu ⇒ _printf_longlong_dec ⇒ _printf_int_common ⇒ _printf_post_padding

[Calls]

- >> _printf_longlong_dec

_printf_llo (Thumb, 0 bytes, Stack size unknown bytes, _printf_llo.o(.ARM.Collect$$_printf_percent$$00000010))

[Stack]

- Max Depth = 56 + Unknown Stack Size
- Call Chain = _printf_llo ⇒ _printf_ll_oct ⇒ _printf_longlong_oct ⇒ _printf_int_common ⇒ _printf_post_padding

[Calls]

- >> _printf_ll_oct

_printf_llx (Thumb, 0 bytes, Stack size unknown bytes, _printf_llx.o(.ARM.Collect$$_printf_percent$$00000011))

[Stack]

- Max Depth = 64 + Unknown Stack Size
- Call Chain = _printf_llx ⇒ _printf_ll_hex ⇒ _printf_longlong_hex ⇒ _printf_int_common ⇒ _printf_post_padding

[Calls]

- >> _printf_ll_hex

_printf_l (Thumb, 0 bytes, Stack size unknown bytes, _printf_l.o(.ARM.Collect$$_printf_percent$$00000012))

_printf_c (Thumb, 0 bytes, Stack size unknown bytes, _printf_c.o(.ARM.Collect$$_printf_percent$$00000013))

[Stack]

- Max Depth = 40 + Unknown Stack Size
- Call Chain = _printf_c ⇒ _printf_char ⇒ _printf_cs_common ⇒ _printf_str ⇒ _printf_post_padding

[Calls]

- >> _printf_char

_printf_s (Thumb, 0 bytes, Stack size unknown bytes, _printf_s.o(.ARM.Collect$$_printf_percent$$00000014))

[Stack]

- Max Depth = 40 + Unknown Stack Size
- Call Chain = _printf_s ⇒ _printf_string ⇒ _printf_cs_common ⇒ _printf_str ⇒ _printf_post_padding

[Calls]

- >> _printf_string

_printf_lc (Thumb, 0 bytes, Stack size unknown bytes, _printf_lc.o(.ARM.Collect$$_printf_percent$$00000015))

[Stack]

- Max Depth = 88 + Unknown Stack Size
- Call Chain = _printf_lc ⇒ _printf_wchar ⇒ _printf_lcs_common ⇒ _printf_wctomb ⇒ _wcrtomb ⇒ __rt_ctype_table

[Calls]

- >> _printf_wchar

_printf_ls (Thumb, 0 bytes, Stack size unknown bytes, _printf_ls.o(.ARM.Collect$$_printf_percent$$00000016))

[Stack]

- Max Depth = 88 + Unknown Stack Size
- Call Chain = _printf_ls ⇒ _printf_wstring ⇒ _printf_lcs_common ⇒ _printf_wctomb ⇒ _wcrtomb ⇒ __rt_ctype_table

[Calls]

- >> _printf_wstring

_printf_percent_end (Thumb, 0 bytes, Stack size unknown bytes, _printf_percent_end.o(.ARM.Collect$$_printf_percent$$00000017))

__rt_lib_init (Thumb, 0 bytes, Stack size unknown bytes, libinit.o(.ARM.Collect$$libinit$$00000000))

[Called By]

- >> __rt_entry_li

__rt_lib_init_fp_1 (Thumb, 0 bytes, Stack size unknown bytes, libinit2.o(.ARM.Collect$$libinit$$00000002))

__rt_lib_init_heap_1 (Thumb, 0 bytes, Stack size unknown bytes, libinit2.o(.ARM.Collect$$libinit$$0000000A))

__rt_lib_init_lc_common (Thumb, 0 bytes, Stack size unknown bytes, libinit2.o(.ARM.Collect$$libinit$$0000000F))

[Calls]

- >> __rt_locale

__rt_lib_init_preinit_1 (Thumb, 0 bytes, Stack size unknown bytes, libinit2.o(.ARM.Collect$$libinit$$00000004))

__rt_lib_init_rand_1 (Thumb, 0 bytes, Stack size unknown bytes, libinit2.o(.ARM.Collect$$libinit$$0000000E))

__rt_lib_init_user_alloc_1 (Thumb, 0 bytes, Stack size unknown bytes, libinit2.o(.ARM.Collect$$libinit$$0000000C))

__rt_lib_init_lc_collate_1 (Thumb, 0 bytes, Stack size unknown bytes, libinit2.o(.ARM.Collect$$libinit$$00000011))

__rt_lib_init_lc_ctype_2 (Thumb, 0 bytes, Stack size unknown bytes, libinit2.o(.ARM.Collect$$libinit$$00000012))

[Stack]

- Max Depth = 8 + Unknown Stack Size
- Call Chain = __rt_lib_init_lc_ctype_2 ⇒ _get_lc_ctype

[Calls]

- >> _get_lc_ctype

__rt_lib_init_lc_ctype_1 (Thumb, 0 bytes, Stack size unknown bytes, libinit2.o(.ARM.Collect$$libinit$$00000013))

__rt_lib_init_lc_monetary_1 (Thumb, 0 bytes, Stack size unknown bytes, libinit2.o(.ARM.Collect$$libinit$$00000015))

__rt_lib_init_lc_numeric_2 (Thumb, 0 bytes, Stack size unknown bytes, libinit2.o(.ARM.Collect$$libinit$$00000016))

[Stack]

- Max Depth = 8 + Unknown Stack Size
- Call Chain = __rt_lib_init_lc_numeric_2 ⇒ _get_lc_numeric

[Calls]

- >> _get_lc_numeric

__rt_lib_init_alloca_1 (Thumb, 0 bytes, Stack size unknown bytes, libinit2.o(.ARM.Collect$$libinit$$0000002E))

__rt_lib_init_argv_1 (Thumb, 0 bytes, Stack size unknown bytes, libinit2.o(.ARM.Collect$$libinit$$0000002C))

__rt_lib_init_atexit_1 (Thumb, 0 bytes, Stack size unknown bytes, libinit2.o(.ARM.Collect$$libinit$$0000001B))

__rt_lib_init_clock_1 (Thumb, 0 bytes, Stack size unknown bytes, libinit2.o(.ARM.Collect$$libinit$$00000021))

__rt_lib_init_cpp_1 (Thumb, 0 bytes, Stack size unknown bytes, libinit2.o(.ARM.Collect$$libinit$$00000032))

__rt_lib_init_exceptions_1 (Thumb, 0 bytes, Stack size unknown bytes, libinit2.o(.ARM.Collect$$libinit$$00000030))

__rt_lib_init_fp_trap_1 (Thumb, 0 bytes, Stack size unknown bytes, libinit2.o(.ARM.Collect$$libinit$$0000001F))

__rt_lib_init_getenv_1 (Thumb, 0 bytes, Stack size unknown bytes, libinit2.o(.ARM.Collect$$libinit$$00000023))

__rt_lib_init_lc_numeric_1 (Thumb, 0 bytes, Stack size unknown bytes, libinit2.o(.ARM.Collect$$libinit$$00000017))

__rt_lib_init_lc_time_1 (Thumb, 0 bytes, Stack size unknown bytes, libinit2.o(.ARM.Collect$$libinit$$00000019))

__rt_lib_init_return (Thumb, 0 bytes, Stack size unknown bytes, libinit2.o(.ARM.Collect$$libinit$$00000033))

__rt_lib_init_signal_1 (Thumb, 0 bytes, Stack size unknown bytes, libinit2.o(.ARM.Collect$$libinit$$0000001D))

__rt_lib_init_stdio_1 (Thumb, 0 bytes, Stack size unknown bytes, libinit2.o(.ARM.Collect$$libinit$$00000025))

__rt_lib_shutdown (Thumb, 0 bytes, Stack size unknown bytes, libshutdown.o(.ARM.Collect$$libshutdown$$00000000))

[Called By]

- >> __rt_exit_ls

__rt_lib_shutdown_cpp_1 (Thumb, 0 bytes, Stack size unknown bytes, libshutdown2.o(.ARM.Collect$$libshutdown$$00000004))

__rt_lib_shutdown_fini_1 (Thumb, 0 bytes, Stack size unknown bytes, libshutdown2.o(.ARM.Collect$$libshutdown$$00000002))

__rt_lib_shutdown_fp_trap_1 (Thumb, 0 bytes, Stack size unknown bytes, libshutdown2.o(.ARM.Collect$$libshutdown$$00000009))

__rt_lib_shutdown_heap_1 (Thumb, 0 bytes, Stack size unknown bytes, libshutdown2.o(.ARM.Collect$$libshutdown$$00000011))

__rt_lib_shutdown_return (Thumb, 0 bytes, Stack size unknown bytes, libshutdown2.o(.ARM.Collect$$libshutdown$$00000012))

__rt_lib_shutdown_signal_1 (Thumb, 0 bytes, Stack size unknown bytes, libshutdown2.o(.ARM.Collect$$libshutdown$$0000000C))

__rt_lib_shutdown_stdio_1 (Thumb, 0 bytes, Stack size unknown bytes, libshutdown2.o(.ARM.Collect$$libshutdown$$00000006))

__rt_lib_shutdown_user_alloc_1 (Thumb, 0 bytes, Stack size unknown bytes, libshutdown2.o(.ARM.Collect$$libshutdown$$0000000E))

__rt_entry (Thumb, 0 bytes, Stack size unknown bytes, __rtentry.o(.ARM.Collect$$rtentry$$00000000))

[Called By]

- >> __main
- >> __scatterload_rt2

__rt_entry_presh_1 (Thumb, 0 bytes, Stack size unknown bytes, __rtentry2.o(.ARM.Collect$$rtentry$$00000002))

__rt_entry_sh (Thumb, 0 bytes, Stack size unknown bytes, __rtentry4.o(.ARM.Collect$$rtentry$$00000004))

[Stack]

- Max Depth = 8 + Unknown Stack Size
- Call Chain = __rt_entry_sh ⇒ __user_setup_stackheap

[Calls]

- >> __user_setup_stackheap

__rt_entry_li (Thumb, 0 bytes, Stack size unknown bytes, __rtentry2.o(.ARM.Collect$$rtentry$$0000000A))

[Calls]

- >> __rt_lib_init

__rt_entry_postsh_1 (Thumb, 0 bytes, Stack size unknown bytes, __rtentry2.o(.ARM.Collect$$rtentry$$00000009))

__rt_entry_main (Thumb, 0 bytes, Stack size unknown bytes, __rtentry2.o(.ARM.Collect$$rtentry$$0000000D))

[Stack]

- Max Depth = 240 + Unknown Stack Size
- Call Chain = __rt_entry_main ⇒ main ⇒ hx711_handle ⇒ hx711_callback ⇒ lcd_printf ⇒ vsprintf ⇒ _printf_char_common ⇒ __printf

[Calls]

- >> main
- >> exit

__rt_entry_postli_1 (Thumb, 0 bytes, Stack size unknown bytes, __rtentry2.o(.ARM.Collect$$rtentry$$0000000C))

__rt_exit (Thumb, 0 bytes, Stack size unknown bytes, rtexit.o(.ARM.Collect$$rtexit$$00000000))

[Called By]

- >> exit

__rt_exit_ls (Thumb, 0 bytes, Stack size unknown bytes, rtexit2.o(.ARM.Collect$$rtexit$$00000003))

[Calls]

- >> __rt_lib_shutdown

__rt_exit_prels_1 (Thumb, 0 bytes, Stack size unknown bytes, rtexit2.o(.ARM.Collect$$rtexit$$00000002))

__rt_exit_exit (Thumb, 0 bytes, Stack size unknown bytes, rtexit2.o(.ARM.Collect$$rtexit$$00000004))

[Calls]

- >> _sys_exit

Reset_Handler (Thumb, 8 bytes, Stack size 0 bytes, startup_stm32f103xb.o(.text))
[Address Reference Count : 1]

- startup_stm32f103xb.o(RESET)

ADC1_2_IRQHandler (Thumb, 0 bytes, Stack size 0 bytes, startup_stm32f103xb.o(.text))

[Calls]

- >> ADC1_2_IRQHandler

[Called By]

- >> ADC1_2_IRQHandler

[Address Reference Count : 1]

- startup_stm32f103xb.o(RESET)

CAN1_RX1_IRQHandler (Thumb, 0 bytes, Stack size 0 bytes, startup_stm32f103xb.o(.text))
[Address Reference Count : 1]

- startup_stm32f103xb.o(RESET)

CAN1_SCE_IRQHandler (Thumb, 0 bytes, Stack size 0 bytes, startup_stm32f103xb.o(.text))
[Address Reference Count : 1]

- startup_stm32f103xb.o(RESET)

DMA1_Channel1_IRQHandler (Thumb, 0 bytes, Stack size 0 bytes, startup_stm32f103xb.o(.text))
[Address Reference Count : 1]

- startup_stm32f103xb.o(RESET)

DMA1_Channel2_IRQHandler (Thumb, 0 bytes, Stack size 0 bytes, startup_stm32f103xb.o(.text))
[Address Reference Count : 1]

- startup_stm32f103xb.o(RESET)

DMA1_Channel3_IRQHandler (Thumb, 0 bytes, Stack size 0 bytes, startup_stm32f103xb.o(.text))
[Address Reference Count : 1]

- startup_stm32f103xb.o(RESET)

DMA1_Channel4_IRQHandler (Thumb, 0 bytes, Stack size 0 bytes, startup_stm32f103xb.o(.text))
[Address Reference Count : 1]

- startup_stm32f103xb.o(RESET)

DMA1_Channel5_IRQHandler (Thumb, 0 bytes, Stack size 0 bytes, startup_stm32f103xb.o(.text))
[Address Reference Count : 1]

- startup_stm32f103xb.o(RESET)

DMA1_Channel6_IRQHandler (Thumb, 0 bytes, Stack size 0 bytes, startup_stm32f103xb.o(.text))
[Address Reference Count : 1]

- startup_stm32f103xb.o(RESET)

DMA1_Channel7_IRQHandler (Thumb, 0 bytes, Stack size 0 bytes, startup_stm32f103xb.o(.text))
[Address Reference Count : 1]

- startup_stm32f103xb.o(RESET)

EXTI0_IRQHandler (Thumb, 0 bytes, Stack size 0 bytes, startup_stm32f103xb.o(.text))
[Address Reference Count : 1]

- startup_stm32f103xb.o(RESET)

EXTI15_10_IRQHandler (Thumb, 0 bytes, Stack size 0 bytes, startup_stm32f103xb.o(.text))
[Address Reference Count : 1]

- startup_stm32f103xb.o(RESET)

EXTI1_IRQHandler (Thumb, 0 bytes, Stack size 0 bytes, startup_stm32f103xb.o(.text))
[Address Reference Count : 1]

- startup_stm32f103xb.o(RESET)

EXTI2_IRQHandler (Thumb, 0 bytes, Stack size 0 bytes, startup_stm32f103xb.o(.text))
[Address Reference Count : 1]

- startup_stm32f103xb.o(RESET)

EXTI3_IRQHandler (Thumb, 0 bytes, Stack size 0 bytes, startup_stm32f103xb.o(.text))
[Address Reference Count : 1]

- startup_stm32f103xb.o(RESET)

EXTI4_IRQHandler (Thumb, 0 bytes, Stack size 0 bytes, startup_stm32f103xb.o(.text))
[Address Reference Count : 1]

- startup_stm32f103xb.o(RESET)

EXTI9_5_IRQHandler (Thumb, 0 bytes, Stack size 0 bytes, startup_stm32f103xb.o(.text))
[Address Reference Count : 1]

- startup_stm32f103xb.o(RESET)

FLASH_IRQHandler (Thumb, 0 bytes, Stack size 0 bytes, startup_stm32f103xb.o(.text))
[Address Reference Count : 1]

- startup_stm32f103xb.o(RESET)

I2C1_ER_IRQHandler (Thumb, 0 bytes, Stack size 0 bytes, startup_stm32f103xb.o(.text))
[Address Reference Count : 1]

- startup_stm32f103xb.o(RESET)

I2C1_EV_IRQHandler (Thumb, 0 bytes, Stack size 0 bytes, startup_stm32f103xb.o(.text))
[Address Reference Count : 1]

- startup_stm32f103xb.o(RESET)

I2C2_ER_IRQHandler (Thumb, 0 bytes, Stack size 0 bytes, startup_stm32f103xb.o(.text))
[Address Reference Count : 1]

- startup_stm32f103xb.o(RESET)

I2C2_EV_IRQHandler (Thumb, 0 bytes, Stack size 0 bytes, startup_stm32f103xb.o(.text))
[Address Reference Count : 1]

- startup_stm32f103xb.o(RESET)

PVD_IRQHandler (Thumb, 0 bytes, Stack size 0 bytes, startup_stm32f103xb.o(.text))
[Address Reference Count : 1]

- startup_stm32f103xb.o(RESET)

RCC_IRQHandler (Thumb, 0 bytes, Stack size 0 bytes, startup_stm32f103xb.o(.text))
[Address Reference Count : 1]

- startup_stm32f103xb.o(RESET)

RTC_Alarm_IRQHandler (Thumb, 0 bytes, Stack size 0 bytes, startup_stm32f103xb.o(.text))
[Address Reference Count : 1]

- startup_stm32f103xb.o(RESET)

RTC_IRQHandler (Thumb, 0 bytes, Stack size 0 bytes, startup_stm32f103xb.o(.text))
[Address Reference Count : 1]

- startup_stm32f103xb.o(RESET)

SPI1_IRQHandler (Thumb, 0 bytes, Stack size 0 bytes, startup_stm32f103xb.o(.text))
[Address Reference Count : 1]

- startup_stm32f103xb.o(RESET)

SPI2_IRQHandler (Thumb, 0 bytes, Stack size 0 bytes, startup_stm32f103xb.o(.text))
[Address Reference Count : 1]

- startup_stm32f103xb.o(RESET)

TAMPER_IRQHandler (Thumb, 0 bytes, Stack size 0 bytes, startup_stm32f103xb.o(.text))
[Address Reference Count : 1]
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

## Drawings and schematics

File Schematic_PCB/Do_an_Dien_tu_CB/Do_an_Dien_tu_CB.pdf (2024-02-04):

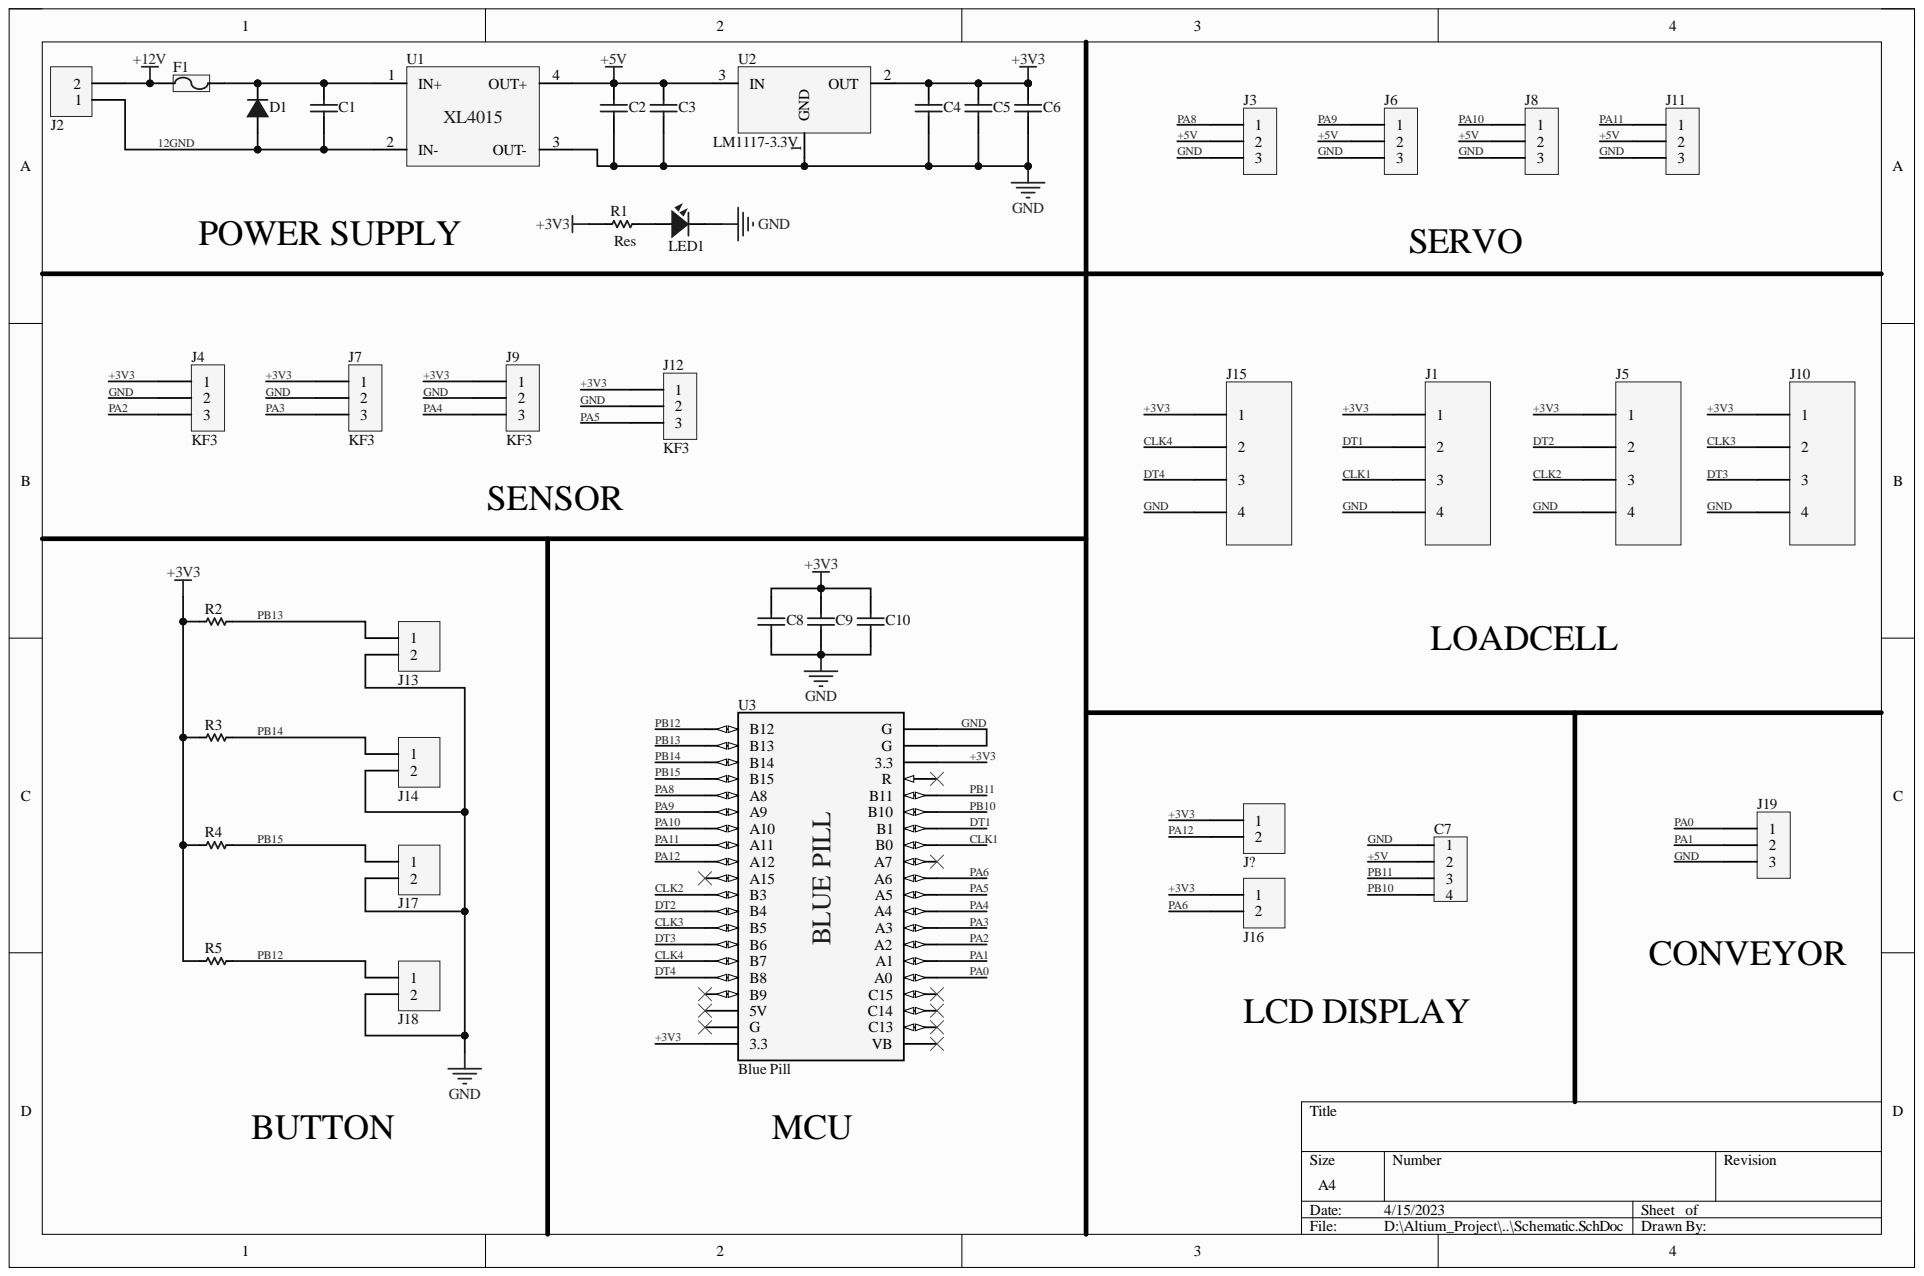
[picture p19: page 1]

Size A4 | Number | Revision

Date: 4/15/2023 | Sheet of
File: D:\Altium_Project\..\Schematic.SchDoc | Drawn By:

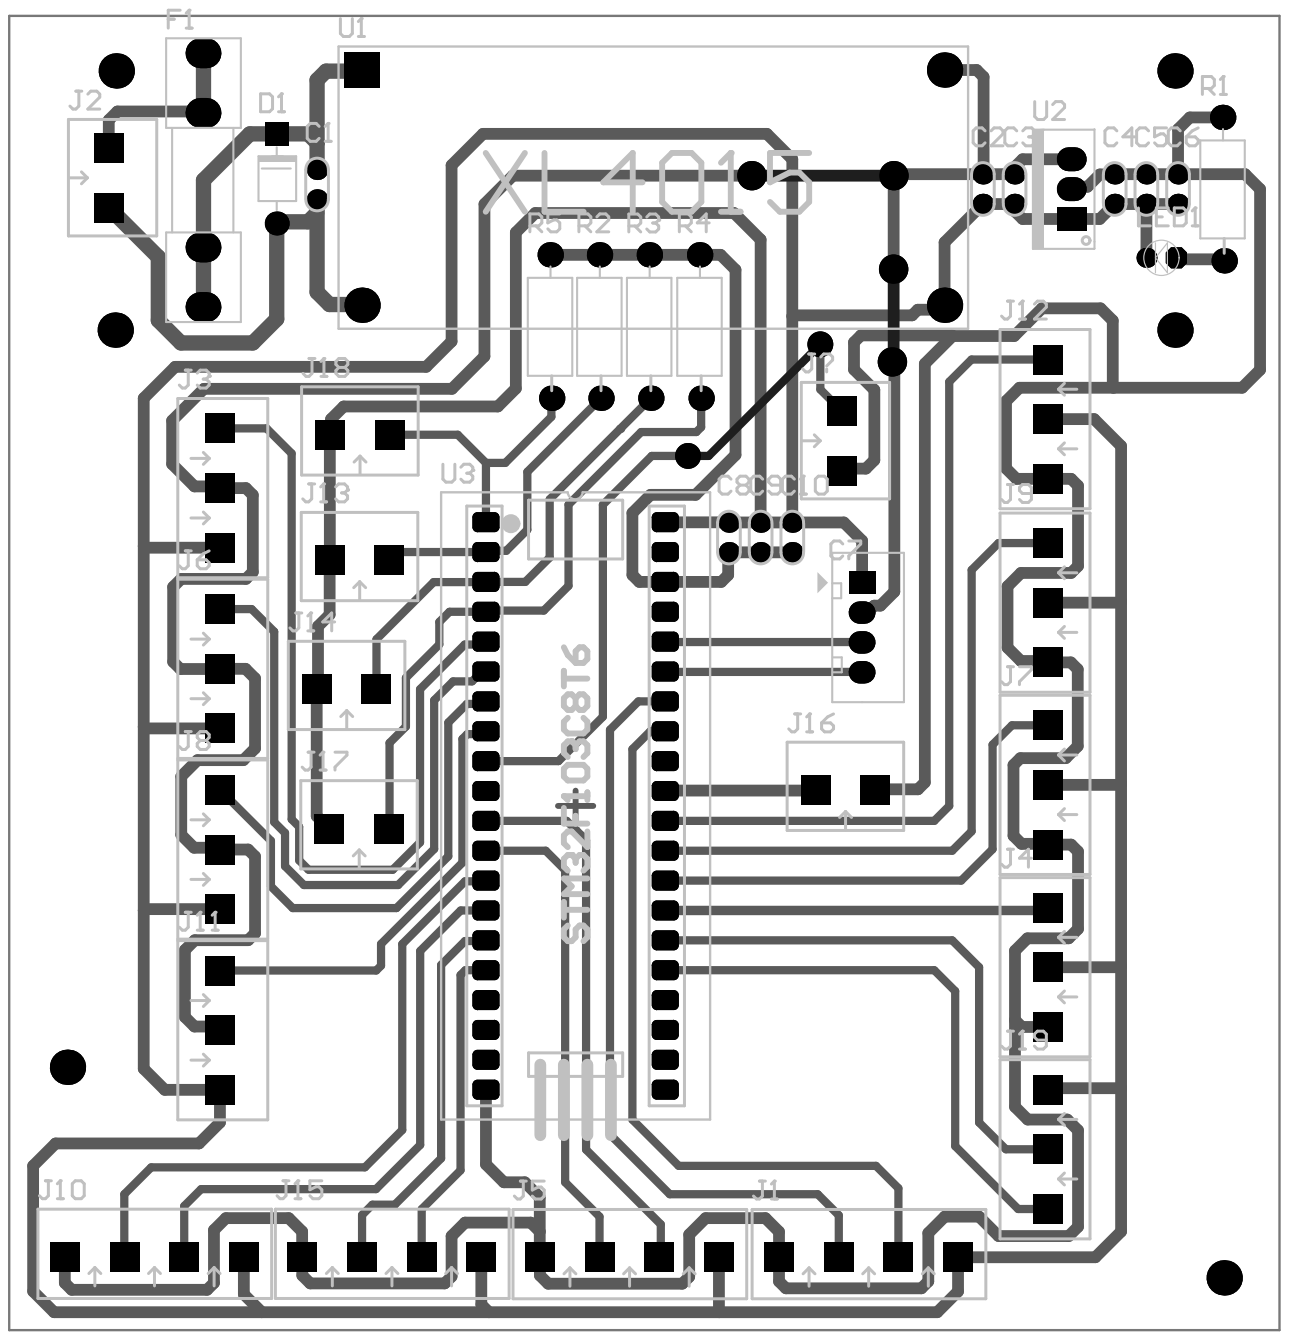
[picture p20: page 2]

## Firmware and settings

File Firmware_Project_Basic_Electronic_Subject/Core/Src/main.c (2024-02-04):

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
/* Includes ------------------------------------------------------------------*/
#include "main.h"
#include "i2c.h"
#include "tim.h"
#include "gpio.h"

/* USER CODE BEGIN Includes */
#include "hx711.h"
#include "Servo.h"
#include "Button.h"
#include "LiquidCrystal_I2C.h"
/* USER CODE END Includes */

/* USER CODE BEGIN PTD */

typedef enum
{
	init_state,
	cat_state,
	xiMang_state,
	nuoc_state,
	da_state,
	finish_state
} system_state_t;

typedef enum
{
	init_st,
	start_st,
	stop_st,
	mac75_st,
	mac200_st
} options_state_t;

/* USER CODE END PTD */

/* USER CODE BEGIN PD */

// Define MAC 75
#define XIMANG75_SETVAL 		(100U)
#define XIMANG75_SETTIMES  	(5U)
#define NUOC75_SETVAL  			(120U)
#define NUOC75_SETTIMES  		(3U)
#define CAT75_SETVAL  			(201U)
#define CAT75_SETTIMES  		(3U)

// Define MAC 200
#define XIMANG200_SETVAL 		(100U)
#define XIMANG200_SETTIMES 	(5U)
#define NUOC200_SETVAL 			(144U)
#define NUOC200_SETTIMES 		(2U)
#define CAT200_SETVAL 			(252U)
#define CAT200_SETTIMES 		(5U)
#define DA200_SETVAL 				(515U)
#define DA200_SETTIMES			(4U)

/* USER CODE END PD */


/* USER CODE BEGIN PV */

static system_state_t sys_state;
static options_state_t op_state;

// Khai bao bien LCD 16x2 + I2C
static LiquidCrystal_I2C lcd;

// Khai bien doi tuong(objects) cho he thong
hx711_t loadcell1, loadcell2, loadcell3, loadcell4;
static servo_typedef_t servo1, servo2, servo3, servo4;
static Button_Typdef cb1, cb2, cb3,cb4, btn_start, btn_stop, btn_mac75, btn_mac200;

// Khoi tao bien de dem so lan can
static uint8_t ui8_cat75Count = 0;
static uint8_t ui8_xiMang75Count = 0;
static uint8_t ui8_nuoc75Count = 0;

static uint8_t ui8_cat200Count = 0;
static uint8_t ui8_xiMang200Count = 0;
static uint8_t ui8_nuoc200Count = 0;
static uint8_t ui8_da200Count = 0;

extern volatile uint8_t ui8_start_var;

/* USER CODE END PV */

void SystemClock_Config(void);
/* USER CODE BEGIN PFP */

// Khai bao nguyen mau ham dieu khien bang tai
static void conveyor_start(void);
static void conveyor_stop(void);

/* USER CODE END PFP */

/* USER CODE BEGIN 0 */

void	btn_pressing_callback(Button_Typdef *ButtonX)
{
	switch (ButtonX->GPIO_Pin)
	{
		case GPIO_PIN_2: // CB 1 - Cat
		{
			// MAC 75
			if (sys_state == cat_state && op_state == mac75_st)
			{
				if (ui8_cat75Count == CAT75_SETTIMES)
				{
					ui8_cat75Count = 0;
					lcd_set_cursor(&lcd, 1,11);
					lcd_printf(&lcd, "%d", ui8_cat75Count);
					sys_state = xiMang_state;
					break;
				}
				conveyor_stop();
				servo_open(&servo1);
				ui8_cat75Count++;
				lcd_set_cursor(&lcd, 0, 9);
				lcd_printf(&lcd, "CAT      ");
				lcd_set_cursor(&lcd, 1,11);
				lcd_printf(&lcd, "%d", ui8_cat75Count);
			}
			// MAC 200
			if (sys_state == cat_state && op_state == mac200_st)
			{
				if (ui8_cat200Count == CAT200_SETTIMES)
				{
					ui8_cat200Count = 0;
					lcd_set_cursor(&lcd, 1,11);
					lcd_printf(&lcd, "%d", ui8_cat200Count);
					sys_state = xiMang_state;
					break;
				}
				conveyor_stop();
				servo_open(&servo1);
				ui8_cat200Count++;
				lcd_set_cursor(&lcd, 0, 9);
				lcd_printf(&lcd, "CAT      ");
				lcd_set_cursor(&lcd, 1,11);
				lcd_printf(&lcd, "%d", ui8_cat200Count);
			}
			break;
		}
		case GPIO_PIN_3: // CB 2 - Xi mang
		{
			// MAC 75
			if (sys_state == xiMang_state && op_state == mac75_st)
			{
				if (ui8_xiMang75Count == XIMANG75_SETTIMES)
				{
					ui8_xiMang75Count = 0;
					lcd_set_cursor(&lcd, 1,11);
					lcd_printf(&lcd, "%d", ui8_xiMang75Count);
					sys_state = nuoc_state;
					break;
				}
				conveyor_stop();
				servo_open(&servo2);
				ui8_xiMang75Count++;
				lcd_set_cursor(&lcd, 0, 9);
				lcd_printf(&lcd, "X.MANG");
				lcd_set_cursor(&lcd, 1,11);
				lcd_printf(&lcd, "%d", ui8_xiMang75Count);
			}
			// MAC 200
			if (sys_state == xiMang_state && op_state == mac200_st)
			{
				if (ui8_xiMang200Count == XIMANG200_SETTIMES)
				{
					ui8_xiMang200Count = 0;
					lcd_set_cursor(&lcd, 1,11);
					lcd_printf(&lcd, "%d", ui8_xiMang200Count);
					sys_state = da_state;
					break;
				}
				conveyor_stop();
				servo_open(&servo2);
				ui8_xiMang200Count++;
				lcd_set_cursor(&lcd, 0, 9);
				lcd_printf(&lcd, "X.MANG");
				lcd_set_cursor(&lcd, 1,11);
				lcd_printf(&lcd, "%d", ui8_xiMang200Count);
			}
			break;
		}
		case GPIO_PIN_4: // CB 3 - Da
		{
			// MAC 75
			if (sys_state == da_state && op_state == mac75_st)
			{
				sys_state = nuoc_state;
			}
			// MAC 200
			if (sys_state == da_state && op_state == mac200_st)
			{
				if (ui8_da200Count == DA200_SETTIMES)
				{
					ui8_da200Count = 0;
					lcd_set_cursor(&lcd, 1,11);
					lcd_printf(&lcd, "%d", ui8_da200Count);
					sys_state = nuoc_state;
					break;
				}
				conveyor_stop();
				servo_open(&servo3);
				ui8_da200Count++;
				lcd_set_cursor(&lcd, 0, 9);
				lcd_printf(&lcd, "DA      ");
				lcd_set_cursor(&lcd, 1,11);
				lcd_printf(&lcd, "%d", ui8_da200Count);
			}

			break;
		}
		case GPIO_PIN_5: // CB 4 - Nuoc
		{
			// MAC 75
			if (sys_state == nuoc_state && op_state == mac75_st)
			{
				conveyor_stop();
				servo_open(&servo4);
				ui8_nuoc75Count++;
				lcd_set_cursor(&lcd, 0, 9);
				lcd_printf(&lcd, "NUOC     ");
				lcd_set_cursor(&lcd, 1,11);
				lcd_printf(&lcd, "%d", ui8_nuoc75Count);
				if (ui8_nuoc75Count == NUOC75_SETTIMES)
				{

					break;
				}
			}
			// MAC 200
			if (sys_state == nuoc_state && op_state == mac200_st)
			{
				conveyor_stop();
				servo_open(&servo4);
				ui8_nuoc200Count++;
				lcd_set_cursor(&lcd, 0, 9);
				lcd_printf(&lcd, "NUOC     ");
				lcd_set_cursor(&lcd, 1,11);
				lcd_printf(&lcd, "%d", ui8_nuoc200Count);
				if (ui8_nuoc200Count == NUOC200_SETTIMES)
				{

					break;
				}
			}
			break;
		}
		case GPIO_PIN_13:
		{
			// START
			HAL_Delay(20);
			lcd_clear_display(&lcd);
			lcd_set_cursor(&lcd, 0, 3);
			lcd_printf(&lcd, "Starting....");
			op_state = start_st;
			break;
		}
		case GPIO_PIN_14:
		{
			// STOP
			if (op_state != start_st)
			{
				op_state = stop_st;
				lcd_clear_display(&lcd);
				HAL_Delay(20);
				lcd_set_cursor(&lcd, 0, 1);
				lcd_printf(&lcd, "<STOPED SYSTEM>");
				lcd_set_cursor(&lcd, 1, 0);
				lcd_printf(&lcd, "->Start to Reset");
			}
			break;
		}
		case GPIO_PIN_15:
		{
			// MAC75
			if (op_state != stop_st)
			{
				op_state = mac75_st;
				sys_state = cat_state;
				lcd_clear_display(&lcd);
				HAL_Delay(20);
				lcd_set_cursor(&lcd, 0, 0);
				lcd_printf(&lcd, "MAC 75 |");
				lcd_set_cursor(&lcd, 1, 0);
				lcd_printf(&lcd, "W: ");
				lcd_set_cursor(&lcd, 1, 9);
				lcd_printf(&lcd, "T: ");
			}
			break;
		}
		case GPIO_PIN_12:
		{
			// MAC200
			if (op_state != stop_st)
			{
				op_state = mac200_st;
				sys_state = cat_state;
				lcd_clear_display(&lcd);
				HAL_Delay(20);
				lcd_set_cursor(&lcd, 0, 0);
				lcd_printf(&lcd, "MAC 200 |");
				lcd_set_cursor(&lcd, 1, 0);
				lcd_printf(&lcd, "W: ");
				lcd_set_cursor(&lcd, 1, 9);
				lcd_printf(&lcd, "T: ");
			}
			break;
		}
	}
}

void btn_press_timeout_callback(Button_Typdef *ButtonX)
{
	if (ButtonX->GPIO_Pin == GPIO_PIN_13)
	{
		NVIC_SystemReset();
	}
}


// -------- Ham callback xu li va dieu khien RC Servo state --------
void hx711_callback(hx711_t *hx711)
{
	//   Begin mode MAC75 
	if (op_state == mac75_st && sys_state != finish_state && sys_state != init_state) // MAC 75
	{
		if (hx711->weight >= (CAT75_SETVAL + 2) && hx711 == &loadcell1) // Cat
		{
			lcd_set_cursor(&lcd, 1,3);
			if (hx711->weight > 0)
				lcd_printf(&lcd, "%.0f", hx711->weight - 4);
			servo_close(&servo1);
			conveyor_start();
		}
		else if (hx711->weight == 0 && hx711 == &loadcell1 && ui8_cat75Count != 0)
		{
			lcd_set_cursor(&lcd, 1,3);
			lcd_printf(&lcd, "   ");
		}
		if (hx711->weight >= (XIMANG75_SETVAL + 2)&& hx711 == &loadcell2)	// Xi mang
		{
			lcd_set_cursor(&lcd, 1,3);
			if (hx711->weight > 0)
				lcd_printf(&lcd, "%.0f", hx711->weight - 4);
			servo_close(&servo2);
			conveyor_start();
		}
		else if (hx711->weight == 0 && hx711 == &loadcell2 && ui8_xiMang75Count != 0)
		{
			lcd_set_cursor(&lcd, 1,3);
			lcd_printf(&lcd, "   ");
		}
		if (hx711->weight >= 0 && hx711 == &loadcell3)	// Ða
		{
	
		}
		if (hx711->weight >= (NUOC75_SETVAL + 2) && hx711 == &loadcell4)	// Nuoc
		{
			lcd_set_cursor(&lcd, 1,3);
			if (hx711->weight > 0)
				lcd_printf(&lcd, "%.0f", hx711->weight - 4);
			servo_close(&servo4);
			if (ui8_nuoc75Count == NUOC75_SETTIMES)
			{
				sys_state = finish_state;
				lcd_set_cursor(&lcd, 1, 0);
				lcd_printf(&lcd, "               ");
				lcd_set_cursor(&lcd, 1, 4);
				lcd_printf(&lcd, "FINISHED");
				ui8_nuoc75Count = 0;
			}
			conveyor_start();
		}
		else if (hx711->weight == 0 && hx711 == &loadcell4 && ui8_nuoc75Count != 0)
		{
			lcd_set_cursor(&lcd, 1,3);
			lcd_printf(&lcd, "   ");
		}
	}
	//   End mode MAC75 
	
	//    Mode MAC 200
	else if (op_state == mac200_st && sys_state != finish_state && sys_state != init_state) // MAC 200
	{
		if (hx711->weight >= (CAT200_SETVAL + 2) && hx711 == &loadcell1) // Cat
		{
			lcd_set_cursor(&lcd, 1,3);
			if (hx711->weight > 0)
				lcd_printf(&lcd, "%.0f", hx711->weight - 4);
			servo_close(&servo1);
			conveyor_start();
		}
		else if (hx711->weight == 0 && hx711 == &loadcell1 && ui8_cat200Count != 0)
		{
			lcd_set_cursor(&lcd, 1,3);
			lcd_printf(&lcd, "   ");
		}
		if (hx711->weight >= (XIMANG200_SETVAL + 2)&& hx711 == &loadcell2)	// Xi mang
		{
			lcd_set_cursor(&lcd, 1,3);
			if (hx711->weight > 0)
				lcd_printf(&lcd, "%.0f", hx711->weight - 4);
			servo_close(&servo2);
			conveyor_start();
		}
		else if (hx711->weight == 0 && hx711 == &loadcell2 && ui8_xiMang200Count != 0)
		{
			lcd_set_cursor(&lcd, 1,3);
			lcd_printf(&lcd, "   ");
		}
		if (hx711->weight >= (DA200_SETVAL + 2) && hx711 == &loadcell3)	// Ða
		{
			lcd_set_cursor(&lcd, 1,3);
			if (hx711->weight > 0)
				lcd_printf(&lcd, "%.0f", hx711->weight - 4);
			servo_close(&servo3);
			conveyor_start();
		}
		else if (hx711->weight == 0 && hx711 == &loadcell3 && ui8_da200Count != 0)
		{
			lcd_set_cursor(&lcd, 1,3);
			lcd_printf(&lcd, "   ");
		}
		if (hx711->weight >= (NUOC200_SETVAL + 2) && hx711 == &loadcell4)	// Nuoc
		{
			lcd_set_cursor(&lcd, 1,3);
			if (hx711->weight > 0)
				lcd_printf(&lcd, "%.0f", hx711->weight - 4);
			servo_close(&servo4);
			if (ui8_nuoc200Count == NUOC200_SETTIMES)
			{
				sys_state = finish_state;
				lcd_set_cursor(&lcd, 1, 0);
				lcd_printf(&lcd, "               ");
				lcd_set_cursor(&lcd, 1, 4);
				lcd_printf(&lcd, "FINISHED");
				ui8_nuoc200Count = 0;
			}
			conveyor_start();
		}
		else if (hx711->weight == 0 && hx711 == &loadcell4 && ui8_nuoc200Count != 0)
		{
			lcd_set_cursor(&lcd, 1,3);
			lcd_printf(&lcd, "   ");
		}
	}
		//   End mode MAC 200
}

/* USER CODE END 0 */

/**
  * @brief  The application entry point.
  * @retval int
  */
int main(void)
{
  /* MCU Configuration--------------------------------------------------------*/

  /* Reset of all peripherals, Initializes the Flash interface and the Systick. */
  HAL_Init();

  /* Configure the system clock */
  SystemClock_Config();

  /* Initialize all configured peripherals */
  MX_GPIO_Init();
  MX_TIM4_Init();
  MX_TIM1_Init();
  MX_TIM2_Init();
  MX_I2C2_Init();
  /* USER CODE BEGIN 2 */
	
	/* Khoi tao LCD 16x2 */
	lcd_init(&lcd, &hi2c2, LCD_ADDR_DEFAULT);
	HAL_Delay(100);
	lcd_set_cursor(&lcd, 0, 2);
	lcd_printf(&lcd, "Press START");
	lcd_set_cursor(&lcd, 1,3);
	lcd_printf(&lcd, "........");
	while(ui8_start_var == 0)
	{
		__NOP;
	}
	op_state = start_st;
	lcd_clear_display(&lcd);
	lcd_set_cursor(&lcd, 0, 1);
	HAL_Delay(10);
	lcd_printf(&lcd, "Cabliration...");
	lcd_set_cursor(&lcd, 1, 1);
	lcd_printf(&lcd, "Initialize....");
	/* Khoi tao trang thai ban dau cua he thong can DL */
	sys_state = init_state;
	
	/* Khoi tao RC Servo */
	HAL_GPIO_WritePin(GPIOC, GPIO_PIN_13, GPIO_PIN_RESET); // Bat dau TB khoi chay he thong
	servo_init(&servo1, &htim1, TIM_CHANNEL_1);
	servo_init(&servo2, &htim1, TIM_CHANNEL_2);
	servo_init(&servo3, &htim1, TIM_CHANNEL_3);
	servo_init(&servo4, &htim1, TIM_CHANNEL_4);
	
	// Khoi tao PWM cho dong co bang chuyen
	HAL_TIM_PWM_Start(&htim2, TIM_CHANNEL_1);
	
	/* Khoi tao nut nhan */
	button_init(&cb1, GPIOA, GPIO_PIN_2);
	button_init(&cb2, GPIOA, GPIO_PIN_3);
	button_init(&cb3, GPIOA, GPIO_PIN_4);
	button_init(&cb4, GPIOA, GPIO_PIN_5);
	button_init(&btn_start, GPIOB, GPIO_PIN_13);
	button_init(&btn_stop, GPIOB, GPIO_PIN_14);
	button_init(&btn_mac75, GPIOB, GPIO_PIN_15);
	button_init(&btn_mac200, GPIOB, GPIO_PIN_12);
	/* Khoi tao trang thai ban dau RC Servo */
	HAL_Delay(500);
	servo_close(&servo1);
	HAL_Delay(500);
	servo_close(&servo2);
	HAL_Delay(500);
	servo_close(&servo3);
	HAL_Delay(500);
	servo_close(&servo4);
	HAL_Delay(200);
	
	/* Cac ham khoi tao Loadcell va cabliration */
	hx711_init(&loadcell1, CLK1_GPIO_Port, CLK1_Pin, DT1_GPIO_Port, DT1_Pin, &htim4);
	hx711_init(&loadcell2, CLK2_GPIO_Port, CLK2_Pin, DT2_GPIO_Port, DT2_Pin, &htim4);
	hx711_init(&loadcell3, CLK3_GPIO_Port, CLK3_Pin, DT3_GPIO_Port, DT3_Pin, &htim4);
	hx711_init(&loadcell4, CLK4_GPIO_Port, CLK4_Pin, DT4_GPIO_Port, DT4_Pin, &htim4);
	HAL_Delay(200); // Waiting complete cablration
	hx711_coef_set(&loadcell1, 1990); 	// 1kg
	hx711_coef_set(&loadcell2, 2260);		// 1kg
	hx711_coef_set(&loadcell3, 442.5);	// 5kg
	hx711_coef_set(&loadcell4, 1965);		// 1kg 
	HAL_Delay(200); // Waiting completely cablration
  hx711_tare(&loadcell1, 10);
	hx711_tare(&loadcell2, 10);
	hx711_tare(&loadcell3, 10);
	hx711_tare(&loadcell4, 10);
	
	HAL_GPIO_WritePin(GPIOC, GPIO_PIN_13, GPIO_PIN_SET);	// Ket thuc TB he thong da chay on dinh
	
	/* Khoi tao trang thai cat cua he thong can DL */
	sys_state = cat_state;
	op_state = init_st;
	conveyor_start();
	HAL_Delay(10);
	lcd_clear_display(&lcd);
	lcd_set_cursor(&lcd, 0, 0);
	lcd_printf(&lcd, "Complete Cablib");
	HAL_Delay(1000);
	lcd_clear_display(&lcd);
	lcd_set_cursor(&lcd, 0, 3);
	lcd_printf(&lcd, "Starting....");
	
	
  /* USER CODE END 2 */

  /* Infinite loop */
  /* USER CODE BEGIN WHILE */
  while (1)
  {
    /* USER CODE END WHILE */

    /* USER CODE BEGIN 3 */
		
		// Cac ham polling de kiem tra cac cam bien quang
		button_handle(&cb1);
		button_handle(&cb2);
		button_handle(&cb3);
		button_handle(&cb4);
		// Cac ham polling de kiem tra nut nhan chon che do
		button_handle(&btn_start);
		button_handle(&btn_stop);
		button_handle(&btn_mac75);
		button_handle(&btn_mac200);
		// Cac ham polling de do can nang
		hx711_handle(&loadcell1);	
		hx711_handle(&loadcell2);
		hx711_handle(&loadcell3);
		hx711_handle(&loadcell4);
  }
  /* USER CODE END 3 */
}

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
/* USER CODE BEGIN 4 */
void conveyor_start(void)
{
	HAL_GPIO_WritePin(GPIOA, GPIO_PIN_1, GPIO_PIN_SET);
	TIM2->CCR1 = 700; // Duty cycle(%) = 70%
}

void conveyor_stop(void)
{
	HAL_GPIO_WritePin(GPIOA, GPIO_PIN_1, GPIO_PIN_RESET);
	TIM2->CCR1 = 1;
}
/* USER CODE END 4 */
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


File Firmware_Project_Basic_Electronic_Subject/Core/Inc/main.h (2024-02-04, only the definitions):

#define PWM_IN1_Pin GPIO_PIN_0
#define PWM_IN1_GPIO_Port GPIOA
#define IN2_Pin GPIO_PIN_1
#define IN2_GPIO_Port GPIOA
#define CLK1_Pin GPIO_PIN_0
#define CLK1_GPIO_Port GPIOB
#define DT1_Pin GPIO_PIN_1
#define DT1_GPIO_Port GPIOB
#define MAC200_Pin GPIO_PIN_12
#define MAC200_GPIO_Port GPIOB
#define START_Pin GPIO_PIN_13
#define START_GPIO_Port GPIOB
#define STOP_Pin GPIO_PIN_14
#define STOP_GPIO_Port GPIOB
#define MAC75_Pin GPIO_PIN_15
#define MAC75_GPIO_Port GPIOB
#define Servo__1_Pin GPIO_PIN_8
#define Servo__1_GPIO_Port GPIOA
#define Servo_2_Pin GPIO_PIN_9
#define Servo_2_GPIO_Port GPIOA
#define Servo_3_Pin GPIO_PIN_10
#define Servo_3_GPIO_Port GPIOA
#define Servo_4_Pin GPIO_PIN_11
#define Servo_4_GPIO_Port GPIOA
#define CLK2_Pin GPIO_PIN_3
#define CLK2_GPIO_Port GPIOB
#define DT2_Pin GPIO_PIN_4
#define DT2_GPIO_Port GPIOB
#define CLK3_Pin GPIO_PIN_5
#define CLK3_GPIO_Port GPIOB
#define DT3_Pin GPIO_PIN_6
#define DT3_GPIO_Port GPIOB
#define CLK4_Pin GPIO_PIN_7
#define CLK4_GPIO_Port GPIOB
#define DT4_Pin GPIO_PIN_8
#define DT4_GPIO_Port GPIOB

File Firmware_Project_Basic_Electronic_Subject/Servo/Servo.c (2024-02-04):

#include "Servo.h"

void servo_init(servo_typedef_t *servo_name, TIM_HandleTypeDef *tim, uint16_t channel)
{
	servo_name->tim_servo = tim;
	servo_name->tim_channel = channel;
	HAL_TIM_PWM_Start(tim, channel);
	servo_name->angle = 0;
}

static uint32_t map(uint32_t x, uint32_t in_min, uint32_t in_max, uint32_t out_min, uint32_t out_max)
{
  return (x - in_min) * (out_max - out_min) / (in_max - in_min) + out_min;
}

void servo_set_angle(servo_typedef_t *servo_name, uint8_t angle)
{
	uint16_t ccr = (uint16_t)map(angle, SERVO_MIN_ANGLE, SERVO_MAX_ANGLE, SERVO_MIN_DUTY, SERVO_MAX_DUTY);
	switch (servo_name->tim_channel)
	{
		case TIM_CHANNEL_1:
		{
			servo_name->tim_servo->Instance->CCR1 = ccr;
			break;
		}
		case TIM_CHANNEL_2:
		{
			servo_name->tim_servo->Instance->CCR2 = ccr;
			break;
		}
		case TIM_CHANNEL_3:
		{
			servo_name->tim_servo->Instance->CCR3 = ccr;
			break;
		}
		case TIM_CHANNEL_4:
		{
			servo_name->tim_servo->Instance->CCR4 = ccr;
			break;
		}
		default:
		{
			
			break;
		}
	}
}

void servo_close(servo_typedef_t *servo_name)
{
	servo_set_angle(servo_name, 0);
}

void servo_open(servo_typedef_t *servo_name)
{
	servo_set_angle(servo_name, 90);
}

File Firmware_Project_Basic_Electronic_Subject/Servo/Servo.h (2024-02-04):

#ifndef SERVO_H
#define SERVO_H

#include "stm32f1xx_hal.h"

#define SERVO_MIN_ANGLE 0
#define SERVO_MAX_ANGLE 180
#define SERVO_MIN_DUTY 500
#define SERVO_MAX_DUTY 2350

typedef struct
{
	TIM_HandleTypeDef *tim_servo;
	uint16_t tim_channel;
	uint8_t angle;
} servo_typedef_t;


void servo_init(servo_typedef_t *servo_name, TIM_HandleTypeDef *tim, uint16_t channel);
void servo_set_angle(servo_typedef_t *servo_name, uint8_t angle);
void servo_close(servo_typedef_t *servo_name);
void servo_open(servo_typedef_t *servo_name);

#endif

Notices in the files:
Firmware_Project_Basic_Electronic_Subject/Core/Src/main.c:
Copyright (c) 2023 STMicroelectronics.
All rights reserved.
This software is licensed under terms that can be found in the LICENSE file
